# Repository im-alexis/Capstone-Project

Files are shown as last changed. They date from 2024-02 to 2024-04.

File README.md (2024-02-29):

# Capstone Project
# Autonomous Plant Watering System Senior Design

Faculty Mentor: Dr. Wei Li

Team Members: Javier Padilla, Alexis Torres, Ian Skillman, Kiet Le, Evan LeBel, Jesus Hernandez, Jaime Sanchez, Rodrigo Romero

Project Description:
Due to changes in the weather and busy work weeks, it can be challenging to keep track of when you last watered your plants. Our Watering System will automate the need to keep track of the last time you watered your plants and give you more time to enjoy seeing your plants grow. This can create longevity in plants including flowers and plants that can feed humans for years to come. 
Specifically, the project will focus on a single unit that contains a small to medium-sized plant. Attached to the unit will be multiple sensors that will detect/measure/record moisture, temperature, humidity, sunlight, and the water level of an in-unit source. Using a Web UI, the user will be able to manually control and set custom watering settings for the unit. 

Team Composition
4 software engineers developing the software that will use algorithms to automate the watering system based on conditions received from the sensors. All of which can be monitored and manually activated on a remote Web UI. 
3 embedded systems engineers working on communication between sensors and microcontroller, as well as any drivers necessary for the attached LCD display or features that are going to be added. Adding additional electronics to power the microcontroller (including a battery pack and solar cell)

Objectives
Embedded Systems Development: Efficient and reliable embedded systems that control hardware components and devices.
Firmware and Software Development: Creating software and firmware to control and interact with hardware components, creating communication with full functionality.
Networking and Communication: Designing systems that can communicate with each other using various communication protocols (TCP or UDP), such as Wi-Fi or Bluetooth.
Test and Validation: Develop test plans and methodologies to ensure that the designed systems and components meet performance and reliability requirements.
Usability and User Experience: Design software interfaces that are user-friendly experience for end-users.
Scalability and Performance: Build software that can handle increased user loads and data info while maintaining optimal performance.
Compatibility: Develop software that is compatible with multiple devices, operating systems, and browsers, to ensure consistent user experience across platforms.
Code Reviews: Collaborative code reviews to maintain code quality, pass knowledge, and resolve code-related issues.
Documentation: Create comprehensive documentation to outline software functionality, architecture, APIs, and usage guidelines.
Data Management: Design a robust data management system to ensure data integrity for software data storage and processing.
Teams
Embedded Systems Team:

Members: Ian Skillman, Evan LeBel, and Jaime Sanchez
Subsystems: Plant Microcontroller, Hub, Wireless, PCB Design
Roles: Firmware/Software, PCB Designer, Hardware Test/Validation, RF, Power, and Data Packet design
Members: 
Ian     - Sensors communication and plant Micro and Water Mechanics
	Evan  - Plant info and Water Mechanics/System Designer/HUB Master/PCB design
	Jaime - Communications/PCB design
Team Timeline:
Checkpoint 1: APIs - TBD
Checkpoint 2: Plant Microcontroller  - TBD
Checkpoint 3: Hub Microcontroller - TBD
Checkpoint 4: Plant-Hub Communication - TBD 
Checkpoint 5: Water Mechanics Design  - TBD
Checkpoint 6: Custom PCB Schematics - TBD 
Checkpoint 7: Final Casing/Housing - TBD

Design Idea:
A plant module will have 3 attached sensors: Light, moisture, and temperature. These sensors will communicate with a custom PCB where the microcontroller will be located. Each plant will have its own sensors and microcontroller, but can also be expanded to accommodate multiple plants per microcontroller. The microcontroller will periodically read the sensors and, based on the sensor data, enable or disable a water pump that delivers water into the plant's soil. The water flow will be fixed, with the amount of water released determined by a time-based factor. The water pump will be connected to a water tank equipped with a sensor to monitor the water level within the tank. This sensor will communicate with the hub, which will be responsible for broadcasting notifications regarding the need to refill the tank. Each microcontroller will communicate with the hub via Bluetooth to periodically send current sensor readings from the plants. The hub can receive multiple data packets from various microcontrollers. Bluetooth will utilize the TCP protocol to prevent interference. The hub will then relay the received data packets over Wi-Fi to be accessed by the PC user for reading and analysis.

Demonstrations of multiple Plant modules per tank/HUB

Software Team: Web Development

Members: Alexis Torres, Kiet Le, Javier Padilla, and Jesus Hernandez
Subsystems: Server / UI - Backend/Front End
Roles:
	Front End Dev: Alexis Torres and Javier Padilla
	Backend Dev: Kiet Le and Jesus Hernandez
Description:
The software team's primary responsibility involves developing the web application, which serves as the user interface for the project. This entails creating a comprehensive, full-stack application capable of storing both user and plant data. Additionally, the software team will manage the critical communication link between the user and the microcontroller.

To ensure a seamless user experience, the team will focus on crafting an intuitive and user-friendly interface, accompanied by an aesthetically pleasing user interface design.

Requirements: 
User Friendly UI
Dark/Light Mode
Language Setting
English
Spanish
Etc.
Account System
Admin Level Control
System Customization
Manual Control
Adding and Configuring Plant Profile
Standard User Level
Monitoring 
Monitoring
Graphical Sensor Data Display
Water Level
Light Detection
Moisture Level
Etc.
System Settings Customization
Custom Plant Profiles
Water Needs
Lights Needs
Data Transmission Rate
New Plant Integration
History
Saving Packets Received from the system
Maintaining History of Notification Events / System Events
Notifications 
SMS
Email
Upscale:
App Development:
Convert the web app into a mobile app that can be accessed on both IOS and Android. 
System Design Draft:
<INPUT PROJECT NAME>
Project Description: <NEEDS WORK>

Team Composition
4 software engineers developing the software that will use algorithms to automate the watering system based on conditions received from the sensors. All of which can be monitored and manually activated on a remote Web UI. 
3 embedded systems engineers working on communication between sensors and microcontroller, as well as any drivers necessary for the attached LCD display or features that are going to be added. Adding additional electronics to power the microcontroller (including a battery pack and solar cell)
Objectives <Fill in Data>
Teams
Embedded Systems Team: <NEED WORK>

Members: Ian Skillman, Evan LeBel, and Jaime Sanchez
Subsystems: Plant Microcontroller, Hub, Wireless, PCB Design
Roles: Firmware/Software, PCB Designer, Hardware Test/Validation, RF, Power, and Data Packet design
Members: 
Ian     - 
	Evan  - 
	Jaime - 
Team Timeline:
Software Team: Web Development

Members: Alexis Torres, Kiet Le, Javier Padilla, and Jesus Hernandez
Subsystems: Server / UI - Backend/Front End
Roles:
	Front End Dev: Alexis Torres and Javier Padilla
	Backend Dev: Kiet Le and Jesus Hernandez
Description:
The software team's primary responsibility involves developing the web application, which shall function as a tool for doctors to monitor patient’s health. This entails creating a comprehensive, full-stack application capable of storing both user and sensor data. Additionally, the software team will manage the critical communication link between the user and the microcontroller. 

To ensure a seamless user experience, the team will focus on crafting an intuitive and user-friendly interface, accompanied by an aesthetically pleasing user interface design.

The goal is to set a framework for health monitoring, where more wearable devices can interface with the web application.  

Requirements: 
User Friendly UI
Dark/Light Mode
Language Setting
English
Spanish
Etc.
Account System
Admin/ Doctor Level Control
System Customization
Manual Control
Adding and Configuring Patient Profile
Standard User Level
Monitoring their own device data
Monitoring
Graphical Sensor Data Display

Etc.
System Settings Customization
Data Transmission Rate
New device integration
History
Saving Packets Received from the system
Maintaining History of Notification Events / System Events
Notifications 
SMS
Email

Upscale:
App Development:
Convert the web app into a mobile app that can be accessed on both IOS and Android. 
Interface for health monitoring wearable devices

System Design Draft:

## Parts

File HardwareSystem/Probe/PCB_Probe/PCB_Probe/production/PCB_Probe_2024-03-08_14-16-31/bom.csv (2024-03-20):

Designator | Footprint | Quantity | Value | LCSC Part #
BT1 | BAT_BH9VPC | 1 | BH9VPC
C1, C10, C9 | C_Disc_D4.7mm_W2.5mm_P5.00mm | 3 | 100nF
C2 | C_Disc_D4.7mm_W2.5mm_P5.00mm | 1 | 10nF
C3 | C_Disc_D4.7mm_W2.5mm_P5.00mm | 1 | 470pF
C4 | C_Disc_D4.7mm_W2.5mm_P5.00mm | 1 | 10uF
D1 | D_DO-35_SOD27_P7.62mm_Horizontal | 1 | 1N4148
H1, H2, H3, H4, H5 | MountingHole_3.2mm_M3 | 5 | MountingHole
J1, J2 | PRT16279 | 2 | Conn_01x15
J3 | PinHeader_1x02_P2.54mm_Vertical | 1 | Conn_01x02_Socket
J4 | PinHeader_1x04_P2.54mm_Vertical | 1 | Conn_01x04_Pin
R1 | R_Axial_DIN0207_L6.3mm_D2.5mm_P10.16mm_Horizontal | 1 | 330R
R2 | R_Axial_DIN0207_L6.3mm_D2.5mm_P10.16mm_Horizontal | 1 | 1.6kR
R3, R6 | R_Axial_DIN0207_L6.3mm_D2.5mm_P10.16mm_Horizontal | 2 | 10kR
R4 | R_Axial_DIN0207_L6.3mm_D2.5mm_P10.16mm_Horizontal | 1 | 1MF
TP1 | TestPoint_Pad_D1.0mm | 1 | 9V Testpoint
TP2 | TestPoint_Pad_D1.0mm | 1 | 3.3V Testpoint
TP4 | TestPoint_Pad_D1.0mm | 1 | 3.3V GND Testpoint
TP5 | TestPoint_Pad_D1.0mm | 1 | Mouisture Testpoint
TP6 | TestPoint_Pad_D1.0mm | 1 | Light Testpoint
U1 | DIP-8_W7.62mm | 1 | TLC555xP

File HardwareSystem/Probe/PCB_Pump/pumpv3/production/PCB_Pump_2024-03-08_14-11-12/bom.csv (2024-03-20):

Designator | Footprint | Quantity | Value | LCSC Part #
5V, 9V, GND | TestPoint_Keystone_5000-5004_Miniature | 3 | TestPoint_Keystone_5000-5004_Miniature
A2 | Arduino_Nano_ESP32_Socket | 1 | Arduino_Nano_ESP32_Socket
C1 | C_Axial_L5.1mm_D3.1mm_P7.50mm_Horizontal | 1 | 0.22 uF
C2 | C_Axial_L5.1mm_D3.1mm_P7.50mm_Horizontal | 1 | 0.1 uF
C3 | C_Axial_L3.8mm_D2.6mm_P7.50mm_Horizontal | 1 | 1nF
C4, C5, C6 | CP_Radial_Tantal_D6.0mm_P2.50mm | 3 | 100uF
D1 | D_DO-35_SOD27_P7.62mm_Horizontal | 1 | 1N914
D2 | D_DO-41_SOD81_P10.16mm_Horizontal | 1 | 1N5819
D3 | D_DO-41_SOD81_P10.16mm_Horizontal | 1 | 1N5817
J1, J2 | PinHeader_1x04_P2.54mm_Vertical | 2 | Conn_01x04_Pin
L1 | L_Axial_L7.0mm_D3.3mm_P10.16mm_Horizontal_Fastron_MICC | 1 | 1000uH
P1_2, P1, P2 | PinHeader_1x02_P2.54mm_Vertical | 3 | PinHeader_1x02_P2.54mm_Vertical
Q1 | IRF510PBF | 1 | IRF510
Q2 | TO-220-3_Vertical | 1 | IRF4905
R1 | R_Axial_DIN0207_L6.3mm_D2.5mm_P7.62mm_Horizontal | 1 | 12k
R2 | R_Axial_DIN0207_L6.3mm_D2.5mm_P7.62mm_Horizontal | 1 | 0.22
R3 | R_Axial_DIN0207_L6.3mm_D2.5mm_P7.62mm_Horizontal | 1 | 180
R4 | R_Axial_DIN0207_L6.3mm_D2.5mm_P7.62mm_Horizontal | 1 | 6.2K
R5 | R_Axial_DIN0207_L6.3mm_D2.5mm_P7.62mm_Horizontal | 1 | 1k
R6 | R_Axial_DIN0207_L6.3mm_D2.5mm_P7.62mm_Horizontal | 1 | 10K
TP1 | TP4056-18650 | 1 | TP4056
U2 | DIP-8_W7.62mm | 1 | MC33063AP
U3 | TO-220-3_Vertical | 1 | LM7805_TO220

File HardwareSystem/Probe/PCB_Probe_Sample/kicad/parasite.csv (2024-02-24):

Comment | Designator | Footprint | LCSC
Battery_Cell | BT1 | kicad:BatteryHolder_Keystone_3002_1x2032
1n | C1 | Capacitor_SMD:C_0402_1005Metric | C1523
100n | C2 | Capacitor_SMD:C_0402_1005Metric | C1525
12p | C3,C4 | Capacitor_SMD:C_0402_1005Metric | C1547
LL4148 | D1 | Diode_SMD:D_MiniMELF | C9808
LED | D2 | LED_SMD:LED_0603_1608Metric | C2286
MMBT3906 | Q1 | Package_TO_SOT_SMD:SOT-23 | C2910191
Q_Photo_NPN | Q4 | snapeda:TR8 | C146233
10k | R1,R4,R7,R8 | Resistor_SMD:R_0402_1005Metric | C25744
470 | R10 | Resistor_SMD:R_0402_1005Metric | C25117
1k | R2 | Resistor_SMD:R_0402_1005Metric | C11702
1M | R6 | Resistor_SMD:R_0402_1005Metric | C26083
B3U-1000P | RST1,SW1 | SW_B3U-1000P | C231329
E73-2G4M08S1C | U1 | snapeda:E73-2G4M08S1C | C356849
SHTC3 | U2 | kicad:Sensirion_DFN-4-1EP_2x2mm_P1mm_EP0.7x1.6mm | C194656
32.768kHz | Y1 | Crystal:Crystal_SMD_3215-2Pin_3.2x1.5mm | C32346

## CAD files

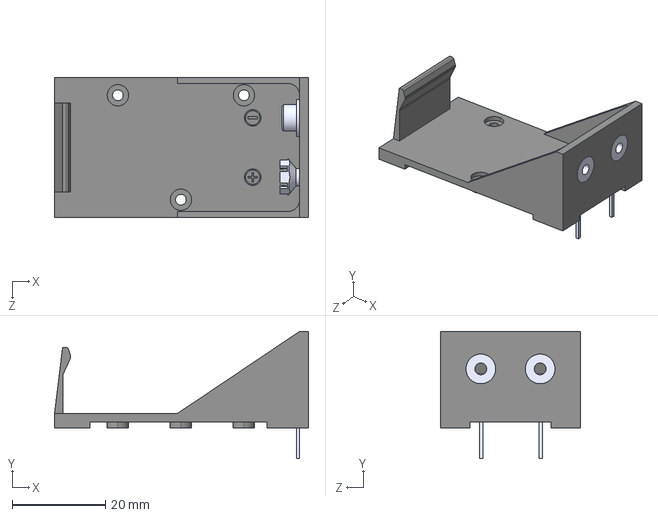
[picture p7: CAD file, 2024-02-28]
HardwareSystem/Probe/Component Library/BH9VPC/BH9VPC.step
54.4 x 27.2 x 30.0 mm

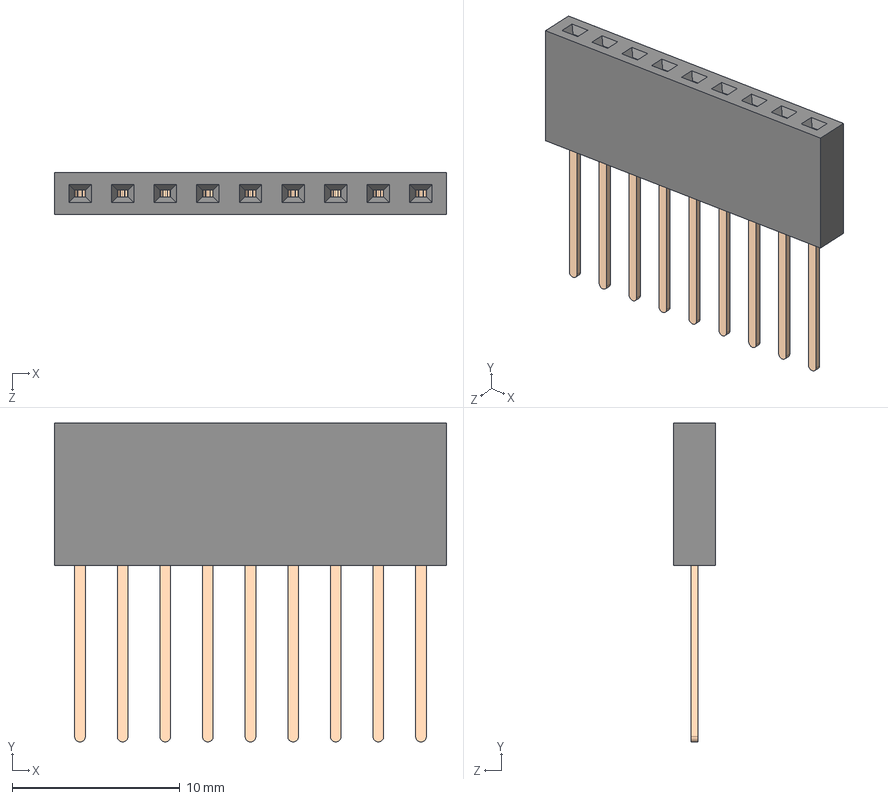
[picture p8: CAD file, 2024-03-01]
HardwareSystem/Probe/Component Library/Headers-PRT-16279/3D/PRT-16279.stp
23.4 x 19.0 x 2.50 mm

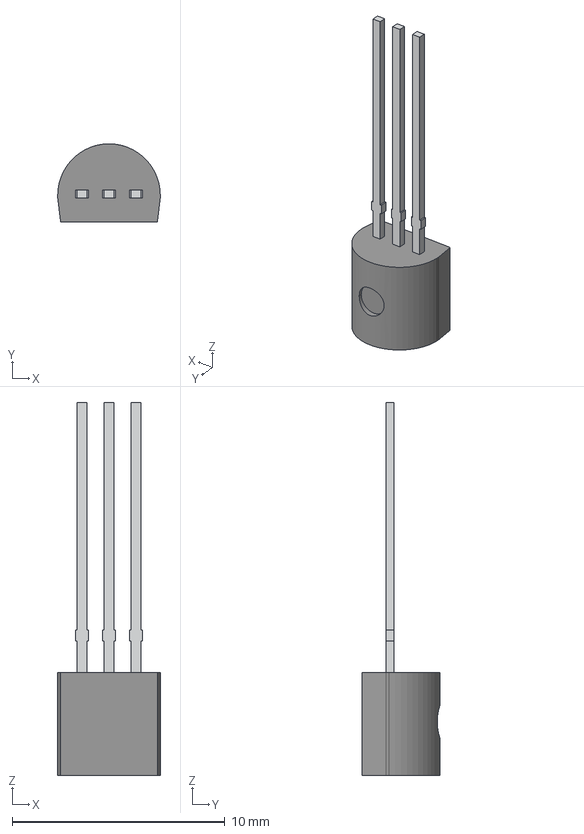
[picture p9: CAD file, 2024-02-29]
HardwareSystem/Probe/Component Library/LP2950CZ_3_0_NOPB/LP0003A.stp
4.83 x 3.68 x 17.5 mm
BODY-TO92
LEAD-TO92 x 3

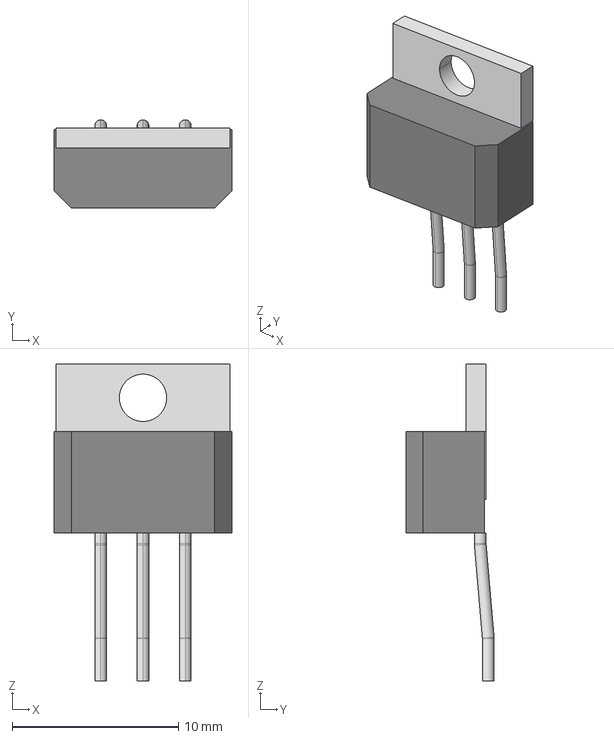
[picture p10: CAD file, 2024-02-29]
HardwareSystem/Probe/Component Library/MCP1825S_3002E_AB/TO-220_AB_MC_MCH.step
10.7 x 5.31 x 19.1 mm

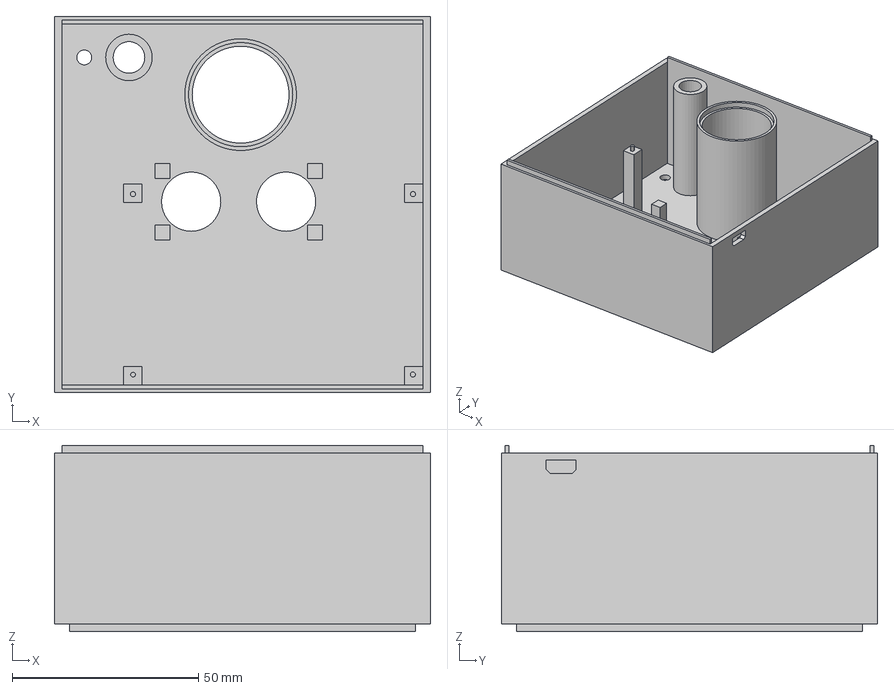
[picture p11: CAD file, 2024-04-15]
HardwareSystem/Probe/Component Library/New_bottom_half.3mf
101.0 x 101.0 x 50.0 mm

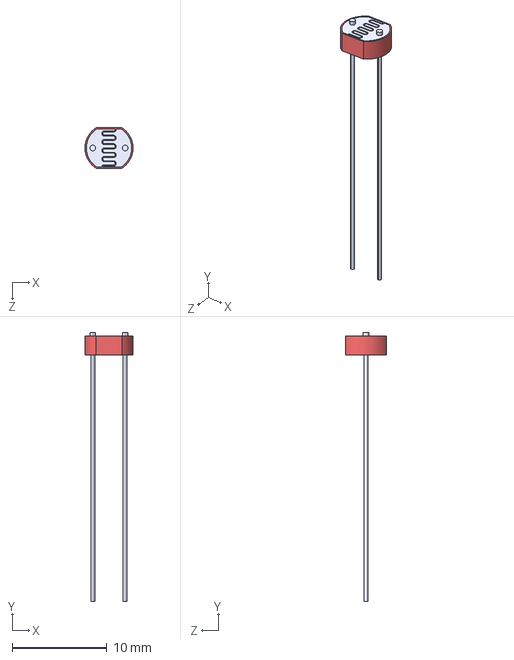
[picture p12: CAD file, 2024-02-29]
HardwareSystem/Probe/Component Library/Photoresistor-161/161.step
5.07 x 28.4 x 4.29 mm

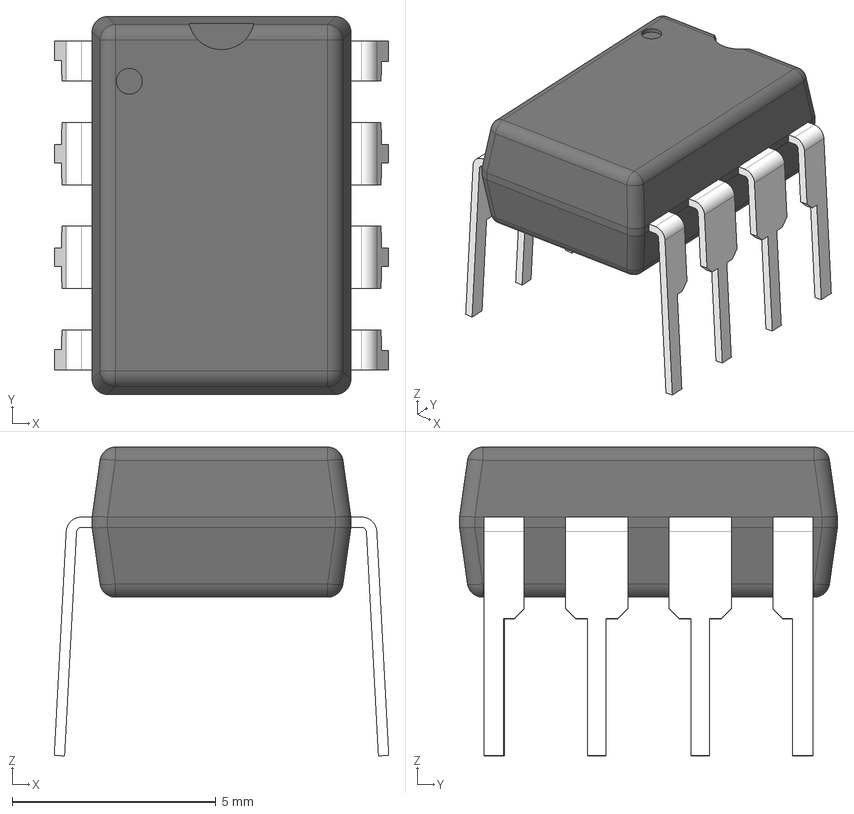
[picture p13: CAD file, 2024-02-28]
HardwareSystem/Probe/PCB_Probe/PCB_Probe/models/ti_TLV5618AIP.stp
8.20 x 9.27 x 7.58 mm
BODY_P0008A
LEAD_P0008A x 4
LD_LHALF_P0008A x 2
LD_RHALF_P0008A x 2

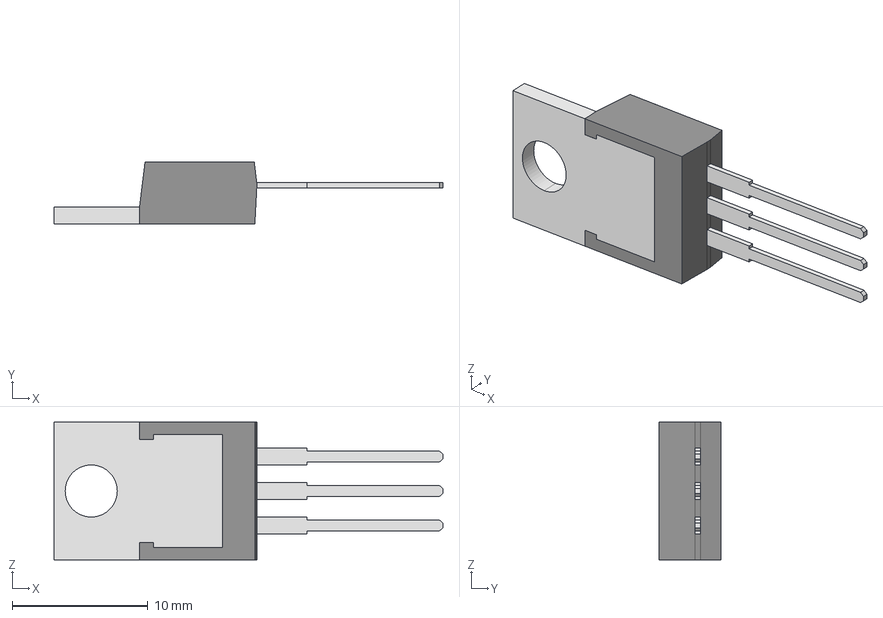
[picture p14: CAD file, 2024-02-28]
HardwareSystem/Probe/PCB_Probe/PCB_Probe/models/LM7805CT_NOPB.stp
28.7 x 4.57 x 10.2 mm
T03B_BODY
T03B_LEAD x 3
T03B_HS

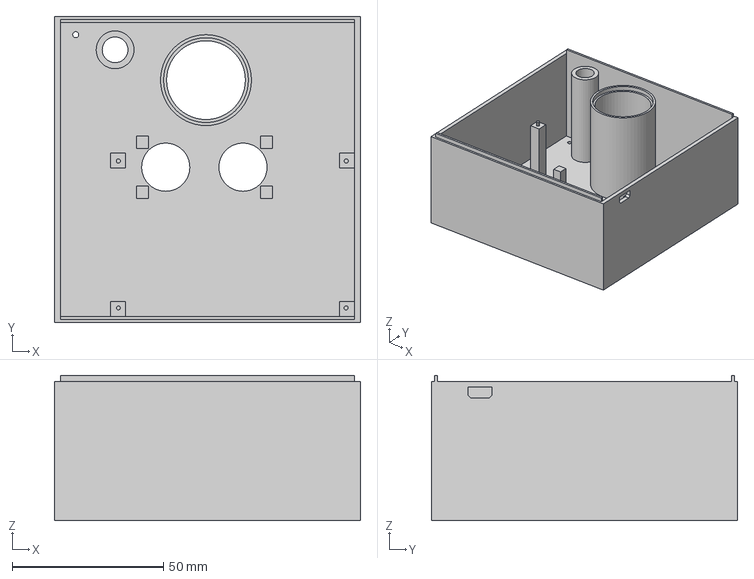
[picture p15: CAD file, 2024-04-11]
HardwareSystem/Probe/Component Library/Hub_Bottom.3mf
101.0 x 101.0 x 48.0 mm

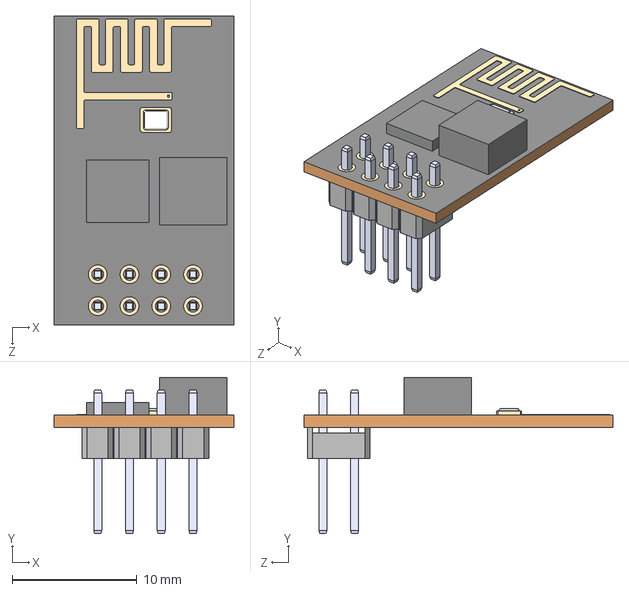
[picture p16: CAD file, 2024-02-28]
HardwareSystem/Probe/PCB_Probe/PCB_Probe/models/ai_thinker_ESP8266-01.step
14.4 x 12.5 x 24.7 mm

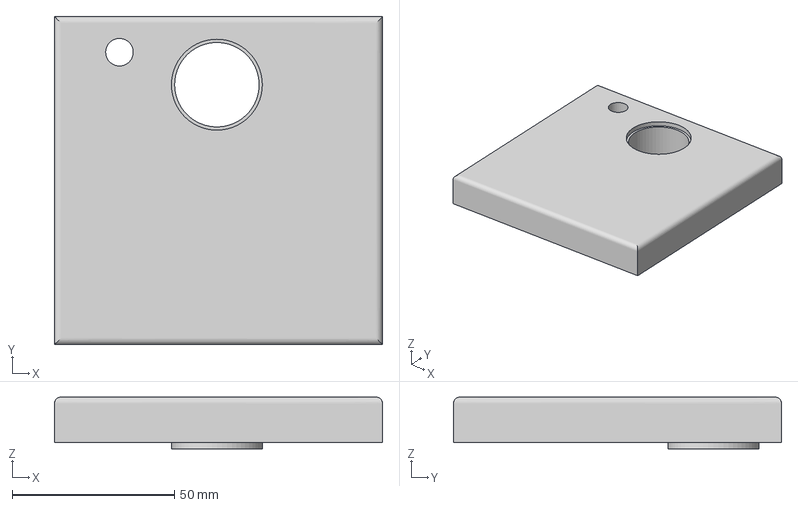
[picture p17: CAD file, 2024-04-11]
HardwareSystem/Probe/Component Library/Hub_Top.3mf
101.0 x 101.0 x 16.0 mm

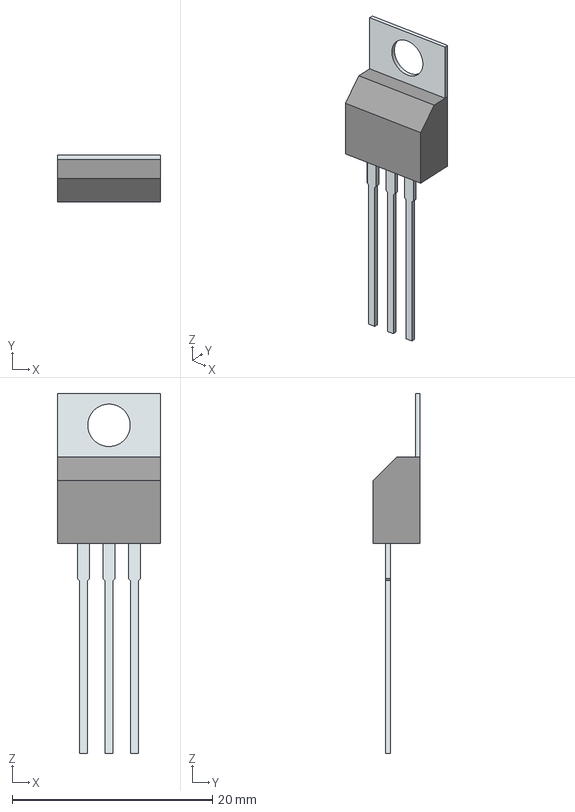
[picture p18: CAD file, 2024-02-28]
HardwareSystem/Probe/PCB_Probe/PCB_Probe/models/LM2937ET-3.3_NOPB.stp
10.3 x 4.70 x 35.9 mm
Tab
PinsArray

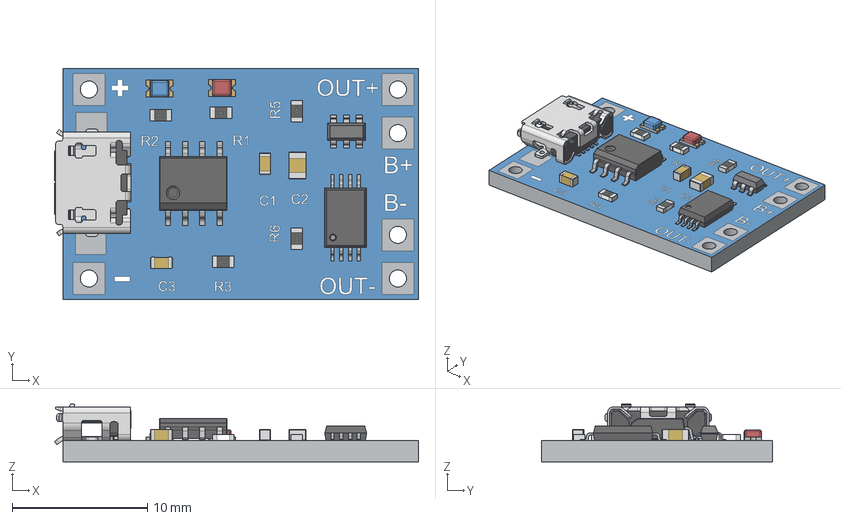
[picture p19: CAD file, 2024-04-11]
HardwareSystem/Probe/Component Library/Lipo Charger - With Load Protection.stp
26.9 x 17.1 x 4.28 mm
bOARD
0603 Capacitor x 2
0603 Resistor x 5
0805 Capacitor
SOIC-8-150
LED - 0805 - Blue
LED - 0805 - Red
USB - Micro
tsop8
sot-23-6-2

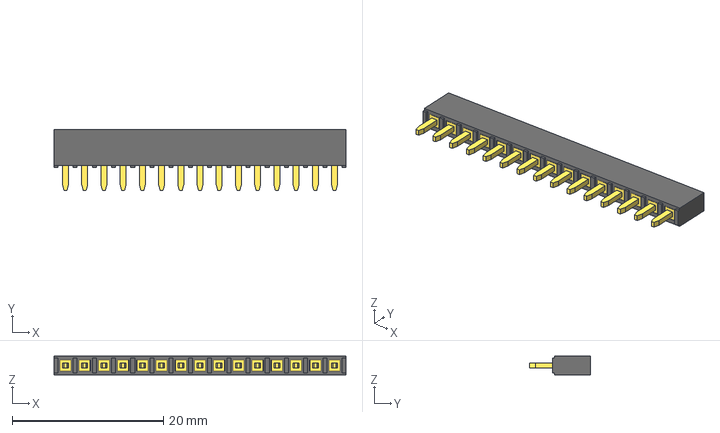
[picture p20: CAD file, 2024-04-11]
HardwareSystem/Probe/Component Library/15-Pin Header - Female - 2.54mm.step
38.6 x 8.00 x 2.50 mm

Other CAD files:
HardwareSystem/Probe/Component Library/Hub_Bottom_Walls.3mf
HardwareSystem/Probe/PCB_Probe/PCB_Probe/models/ti_LM4041CILPR.step
HardwareSystem/Probe/PCB_Probe/PCB_Probe/models/adafruit_st7735r.stp
HardwareSystem/Probe/PCB_Probe/PCB_Probe/models/vishay_IRLD024PBF.stp
HardwareSystem/Probe/Component Library/Hub_Bottom.stl
HardwareSystem/Probe/PCB_Probe/PCB_Probe/models/COM-16473.stp

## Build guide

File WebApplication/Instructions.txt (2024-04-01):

ALWAYS WORK IN A VIRTUAL ENVIRONMENT - When Developing backend

TO CREATE A VIRTUAL ENVIRONMENT: (pip or pip3)
pip install virtualenv
python<version> -m venv <virtual-environment-name>

TO ACTIVATE THE ENVIRONMENT:
source <virtual-environment-name>/bin/activate

TO INSTALL LIBRARIES:
pip install -r requirements.txt  

IF YOU ADD NEW LIBRARIES:
pip freeze > requirements.txt

TO CLOSE THE VIRTUAL ENVIRONMENT:
deactivate

DATABASE AND ROUTES DEFINITION
https://docs.google.com/document/d/1mbG9H52PVBVGft23lnzvOi_USRNvHaWslcnwI_Q0cF0/edit?usp=sharing

TO START backend
cd WebApplication/backend
flask --app app run

TO START frontend
cd WebApplication/frontend/apws
npm start

To Test With HARDWARE
Launch backend using python app.py

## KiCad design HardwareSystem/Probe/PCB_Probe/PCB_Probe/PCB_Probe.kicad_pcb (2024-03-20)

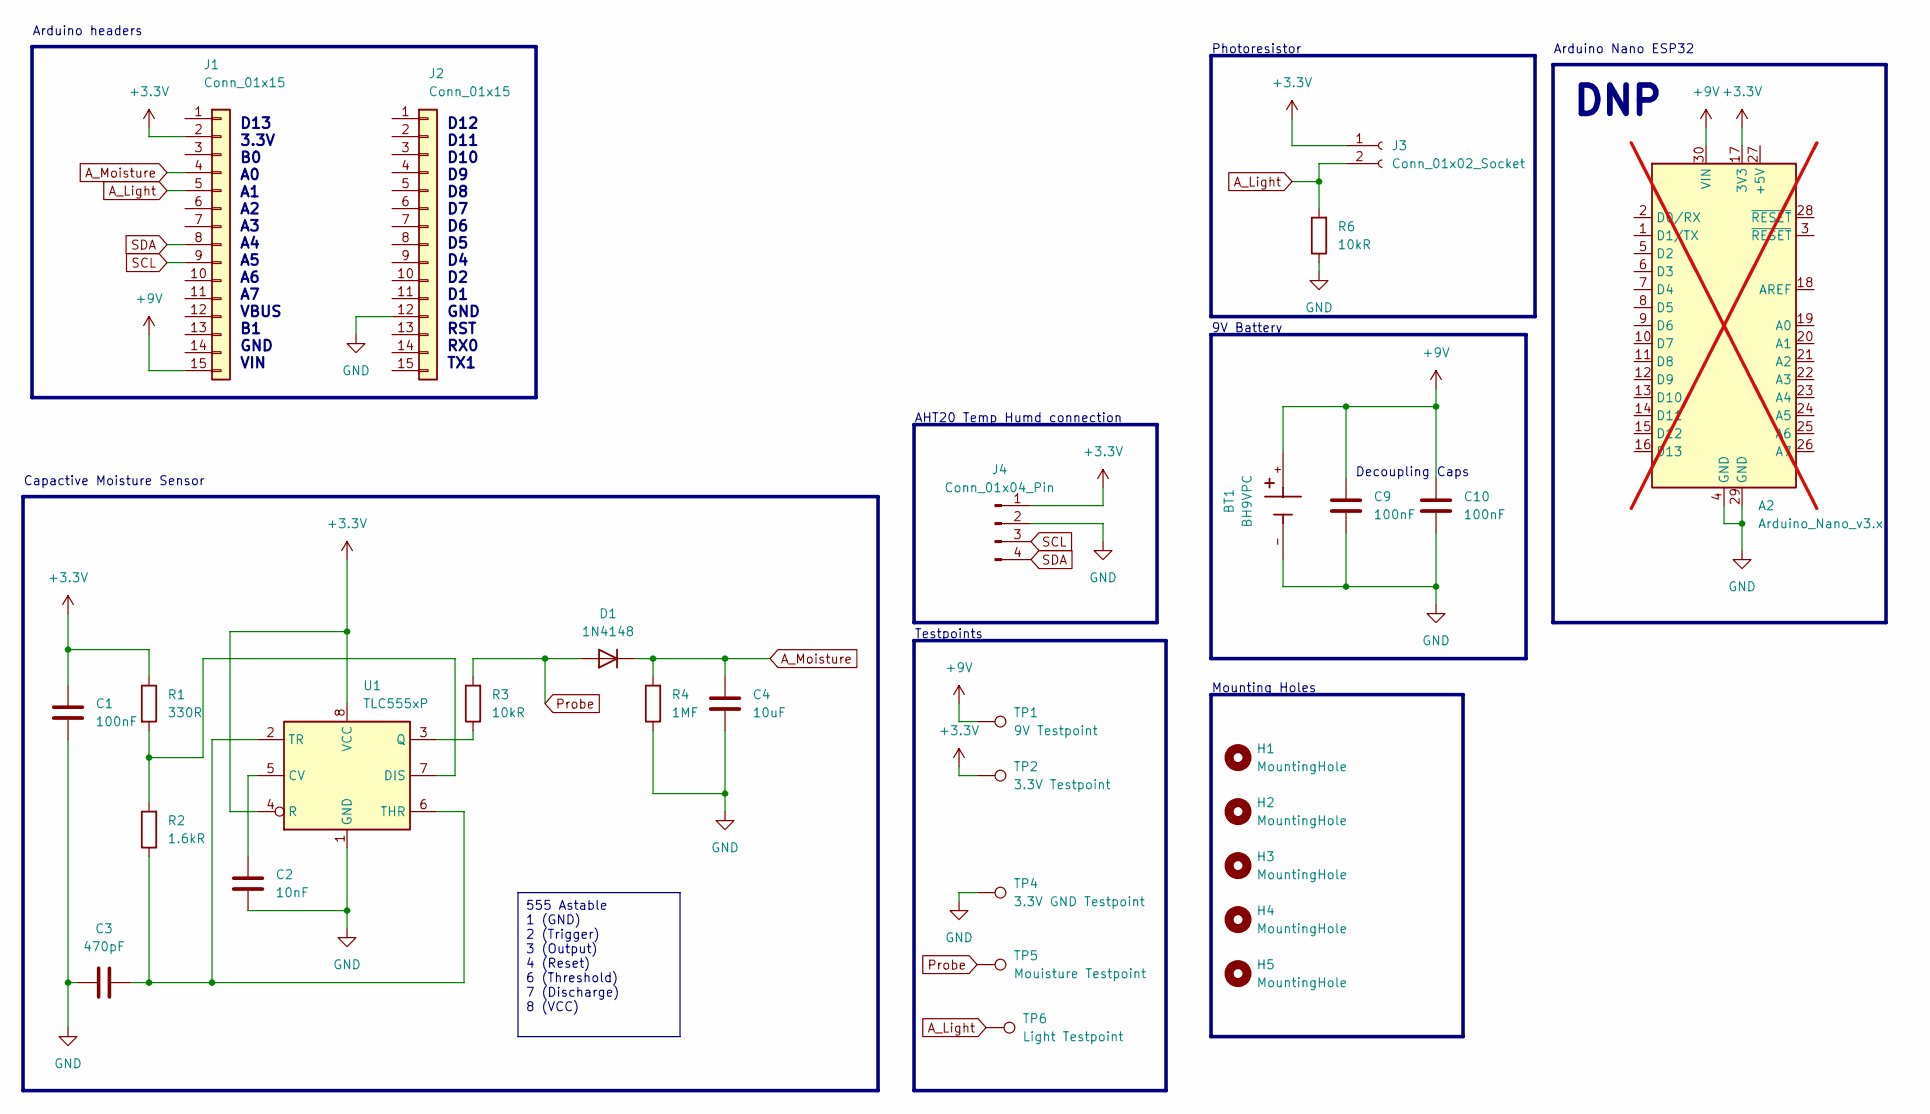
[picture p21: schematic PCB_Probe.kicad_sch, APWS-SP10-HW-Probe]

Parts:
A2: Arduino_Nano_v3.x; Arduino_Nano; not fitted
BT1: BH9VPC; BAT_BH9VPC; PARTREV F
C1, C9, C10: 100nF; C_Disc_D4.7mm_W2.5mm_P5.00mm
C2: 10nF; C_Disc_D4.7mm_W2.5mm_P5.00mm
C3: 470pF; C_Disc_D4.7mm_W2.5mm_P5.00mm
C4: 10uF; C_Disc_D4.7mm_W2.5mm_P5.00mm
D1: 1N4148; D_DO-35_SOD27_P7.62mm_Horizontal
H1, H2, H3, H4, H5: MountingHole; MountingHole_3.2mm_M3
J1, J2: Conn_01x15; PRT16279
J3: Conn_01x02_Socket; PinHeader_1x02_P2.54mm_Vertical
J4: Conn_01x04_Pin; PinHeader_1x04_P2.54mm_Vertical
R1: 330R; R_Axial_DIN0207_L6.3mm_D2.5mm_P10.16mm_Horizontal
R2: 1.6kR; R_Axial_DIN0207_L6.3mm_D2.5mm_P10.16mm_Horizontal
R3, R6: 10kR; R_Axial_DIN0207_L6.3mm_D2.5mm_P10.16mm_Horizontal
R4: 1MF; R_Axial_DIN0207_L6.3mm_D2.5mm_P10.16mm_Horizontal
TP1: 9V Testpoint; TestPoint_Pad_D1.0mm
TP2: 3.3V Testpoint; TestPoint_Pad_D1.0mm
TP4: 3.3V GND Testpoint; TestPoint_Pad_D1.0mm
TP5: Mouisture Testpoint; TestPoint_Pad_D1.0mm
TP6: Light Testpoint; TestPoint_Pad_D1.0mm
U1: TLC555xP; DIP-8_W7.62mm

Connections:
+3.3V: A2.17 (3V3), C1.2, J1.2, J3.1, J4.1, R1.1, TP2.1, U1.4 (R), U1.8 (VCC)
+9V: A2.30 (VIN), BT1.+, C9.1, C10.1, J1.15, TP1.1
A_Light: J1.5, J3.2, R6.2, TP6.1
A_Moisture: C4.1, D1.1 (K), J1.4, R4.2
GND: A2.4 (GND), A2.29 (GND), BT1.-, C1.1, C2.2, C3.1, C4.2, C9.2, C10.2, J2.12, J4.2, R4.1, R6.1, TP4.1, U1.1 (GND)
unnamed: C2.1, U1.5 (CV)
unnamed: R1.2, R2.2, U1.7 (DIS)
unnamed: R3.1, U1.3 (Q)
unnamed: C3.2, R2.1, U1.2 (TR), U1.6 (THR)
Probe: D1.2 (A), R3.2, TP5.1
SCL: J1.9, J4.3
SDA: J1.8, J4.4

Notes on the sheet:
555 Astable 1 (GND) 2 (Trigger) 3 (Output) 4 (Reset) 6 (Threshold) 7 (Discharge) 8 (VCC)
9V Battery
AHT20 Temp Humd connection
DNP
Testpoints
Arduino Nano ESP32
D13 3.3V B0 A0 A1 A2 A3 A4 A5 A6 A7 VBUS B1 GND VIN
Arduino headers
Photoresistor
Mounting Holes
Capactive Moisture Sensor
Decoupling Caps
D12 D11 D10 D9 D8 D7 D6 D5 D4 D2 D1 GND RST RX0 TX1

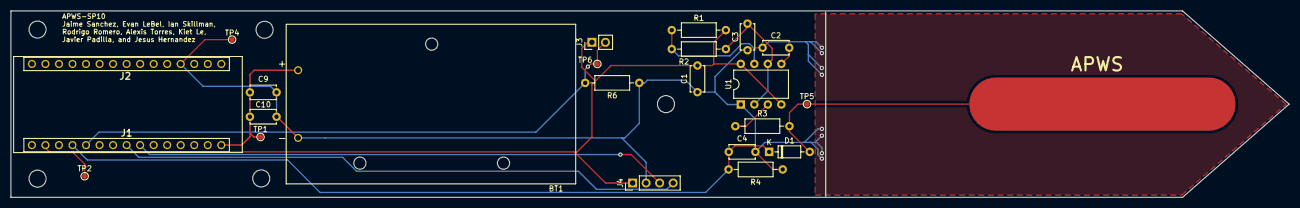
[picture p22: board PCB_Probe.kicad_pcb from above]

Board: 2 copper layers, 240.0 x 35.0 mm, 28 parts (0 on the bottom side), 12 nets.

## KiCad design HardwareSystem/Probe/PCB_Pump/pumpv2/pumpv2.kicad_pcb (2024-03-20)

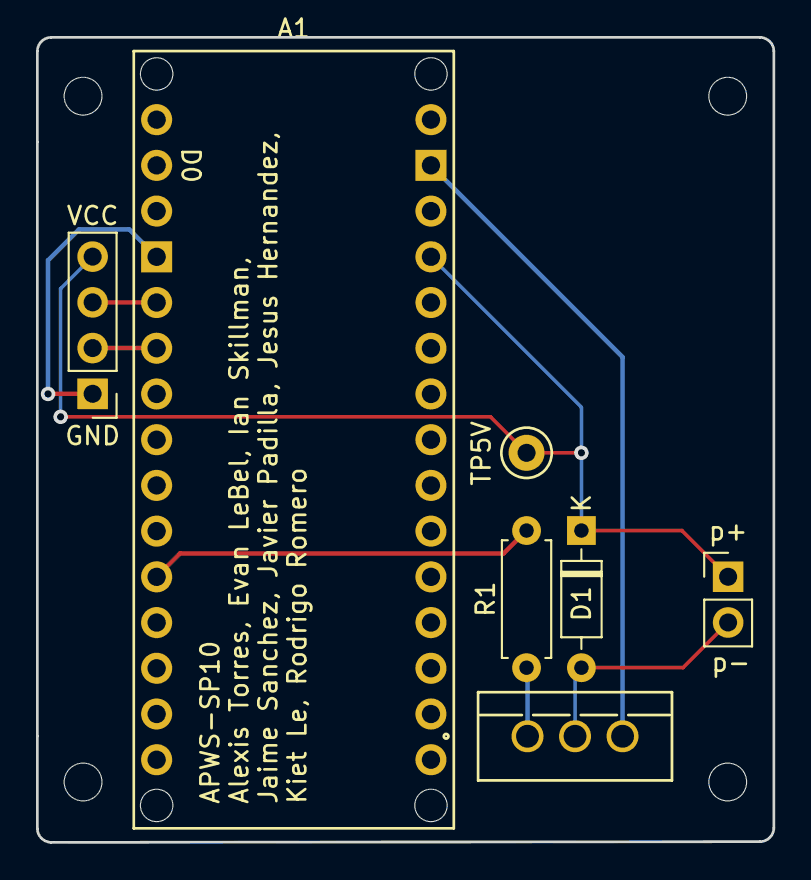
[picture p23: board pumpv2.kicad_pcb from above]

Board: 2 copper layers, 40.9 x 44.7 mm, 7 parts (0 on the bottom side), 5 nets.

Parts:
A1: Arduino_Nano_ESP32_Socket
D1: 1N914; D_DO-35_SOD27_P7.62mm_Horizontal
GND: Conn_01x04_Pin; PinHeader_1x04_P2.54mm_Vertical
Q1: IRF510; IRF510PBF
R1: 12k; R_Axial_DIN0207_L6.3mm_D2.5mm_P7.62mm_Horizontal
TP5V: TestPoint_Keystone_5000-5004_Miniature
p+: PinHeader_1x02_P2.54mm_Vertical

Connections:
GND: A1.GND1 (GND), A1.GND2 (GND), Q1.3 (S)
unnamed: A1.D8, R1.1
unnamed: Q1.1 (G), R1.2
pump+: A1.5V, D1.1 (K)
pump-: D1.2 (A), Q1.2 (D)

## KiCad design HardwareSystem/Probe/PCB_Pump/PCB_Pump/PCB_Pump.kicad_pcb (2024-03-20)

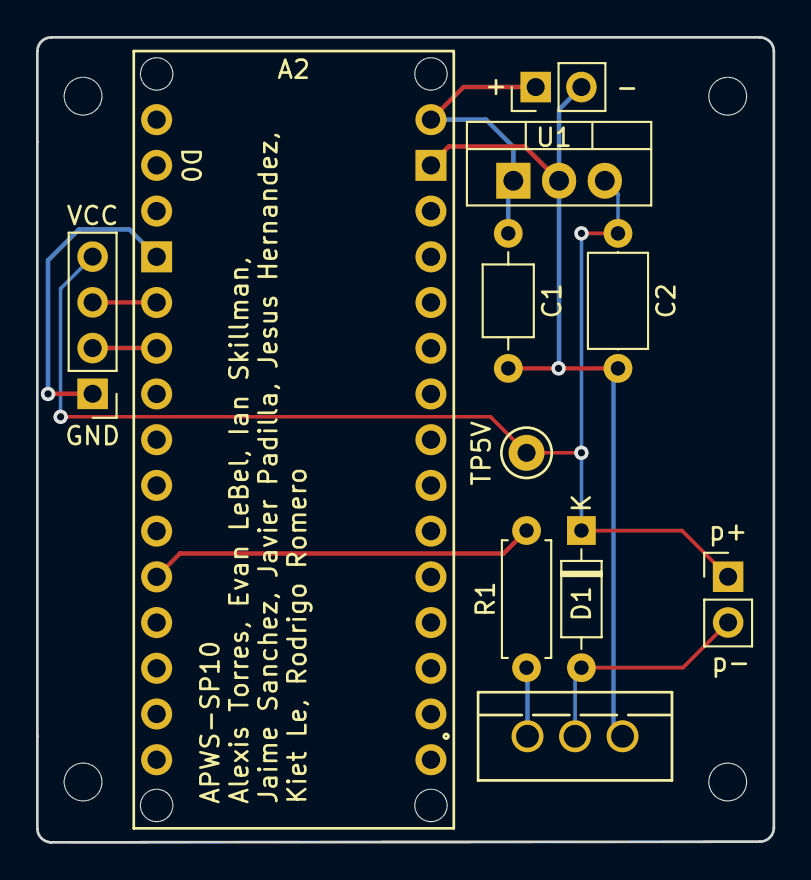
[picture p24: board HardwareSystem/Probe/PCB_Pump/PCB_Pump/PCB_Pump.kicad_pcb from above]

Board: 2 copper layers, 40.9 x 44.7 mm, 11 parts (0 on the bottom side), 8 nets.

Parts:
+: PinHeader_1x02_P2.54mm_Vertical
A2: Arduino_Nano_ESP32_Socket
C1: 0.1 uF; C_Axial_L3.8mm_D2.6mm_P7.50mm_Horizontal
C2: 10 uF; C_Axial_L5.1mm_D3.1mm_P7.50mm_Horizontal
D1: 1N914; D_DO-35_SOD27_P7.62mm_Horizontal
GND: Conn_01x04_Pin; PinHeader_1x04_P2.54mm_Vertical
Q1: IRF510; IRF510PBF
R1: 12k; R_Axial_DIN0207_L6.3mm_D2.5mm_P7.62mm_Horizontal
TP5V: TestPoint_Keystone_5000-5004_Miniature
U1: LM2937xT; TO-220-3_Vertical
p+: PinHeader_1x02_P2.54mm_Vertical

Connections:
9V: +.1, A2.VIN, C1.1, U1.1 (VI)
Echo: A2.D3, GND.2
GND: +.2, A2.GND1 (GND), A2.GND2 (GND), C1.2, C2.2, GND.1, Q1.3 (S), U1.2 (GND)
unnamed: A2.D8, R1.1
unnamed: Q1.1 (G), R1.2
Trig: A2.D2, GND.3
pump+: C2.1, D1.1 (K), GND.4, TP5V.1, U1.3 (VO), p+.1
pump-: D1.2 (A), Q1.2 (D), p+.2

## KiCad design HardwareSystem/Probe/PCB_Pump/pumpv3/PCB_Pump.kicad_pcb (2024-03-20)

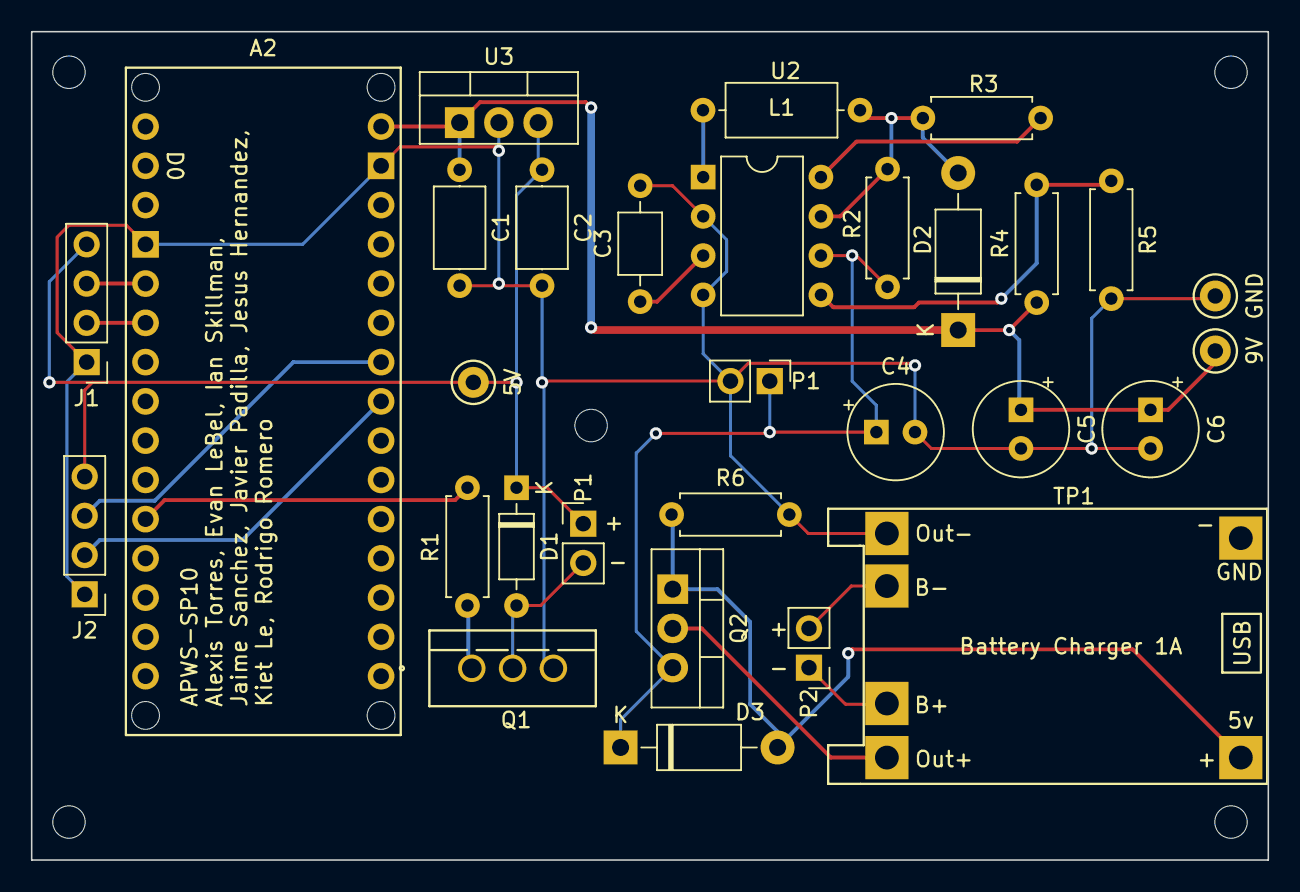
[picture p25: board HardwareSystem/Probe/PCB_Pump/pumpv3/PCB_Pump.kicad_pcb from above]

Board: 2 copper layers, 80.0 x 53.6 mm, 30 parts (0 on the bottom side), 20 nets.

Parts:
5V, 9V: TestPoint_Keystone_5000-5004_Miniature
A2: Arduino_Nano_ESP32_Socket
C1: 0.22 uF; C_Axial_L5.1mm_D3.1mm_P7.50mm_Horizontal
C2: 0.1 uF; C_Axial_L5.1mm_D3.1mm_P7.50mm_Horizontal
C3: 1nF; C_Axial_L3.8mm_D2.6mm_P7.50mm_Horizontal
C4, C5, C6: 100uF; CP_Radial_Tantal_D6.0mm_P2.50mm
D1: 1N914; D_DO-35_SOD27_P7.62mm_Horizontal
D2: 1N5819; D_DO-41_SOD81_P10.16mm_Horizontal
D3: 1N5817; D_DO-41_SOD81_P10.16mm_Horizontal
GND: TestPoint_Keystone_5000-5004_Miniature
J1, J2: Conn_01x04_Pin; PinHeader_1x04_P2.54mm_Vertical
L1: 1000uH; L_Axial_L7.0mm_D3.3mm_P10.16mm_Horizontal_Fastron_MICC
P1, P1#2, P2: PinHeader_1x02_P2.54mm_Vertical
Q1: IRF510; IRF510PBF
Q2: IRF4905; TO-220-3_Vertical
R1: 12k; R_Axial_DIN0207_L6.3mm_D2.5mm_P7.62mm_Horizontal
R2: 0.22; R_Axial_DIN0207_L6.3mm_D2.5mm_P7.62mm_Horizontal
R3: 180; R_Axial_DIN0207_L6.3mm_D2.5mm_P7.62mm_Horizontal
R4: 6.2K; R_Axial_DIN0207_L6.3mm_D2.5mm_P7.62mm_Horizontal
R5: 1k; R_Axial_DIN0207_L6.3mm_D2.5mm_P7.62mm_Horizontal
R6: 10K; R_Axial_DIN0207_L6.3mm_D2.5mm_P7.62mm_Horizontal
TP1: TP4056; TP4056-18650
U2: MC33063AP; DIP-8_W7.62mm
U3: LM7805_TO220; TO-220-3_Vertical

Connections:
3V7+: C4.1, D3.1 (K), P1#2.1, Q2.3 (S), R2.2, U2.6 (Vin)
3V7-: A2.GND1 (GND), A2.GND2 (GND), C1.2, C2.2, C3.2, C4.2, C5.2, C6.2, GND.1, J1.1, J2.1, P1#2.2, Q1.3 (S), R5.2, R6.2, TP1.4 (out-), U2.2 (SwE), U2.4 (GND), U3.2 (GND)
9V: 9V.1, A2.VIN, C1.1, C5.1, C6.1, D2.1 (K), R4.1, U3.1 (VI)
Batt+: P2.1, TP1.5 (B+)
Batt-: P2.2, TP1.6 (B-)
Echo: A2.D3, J1.2
unnamed: A2.D8, R1.1
unnamed: D2.2 (A), L1.1, R2.1, R3.2, U2.7 (Ipk)
unnamed: D3.2 (A), Q2.1 (G), R6.1, TP1.1 (in+)
unnamed: Q1.1 (G), R1.2
unnamed: Q2.2 (D), TP1.3 (out+)
unnamed: R3.1, U2.8 (DC)
unnamed: L1.2, U2.1 (SwC)
unnamed: C3.1, U2.3 (TC)
P5: R4.2, R5.1, U2.5 (Vfb)
SCL: A2.A5 (A5/SCL), J2.3
SDA: A2.A4 (A4/SDA), J2.2
Trig: A2.D2, J1.3
pump+: 5V.1, C2.1, D1.1 (K), J1.4, J2.4, P1.1, U3.3 (VO)
pump-: D1.2 (A), P1.2, Q1.2 (D)

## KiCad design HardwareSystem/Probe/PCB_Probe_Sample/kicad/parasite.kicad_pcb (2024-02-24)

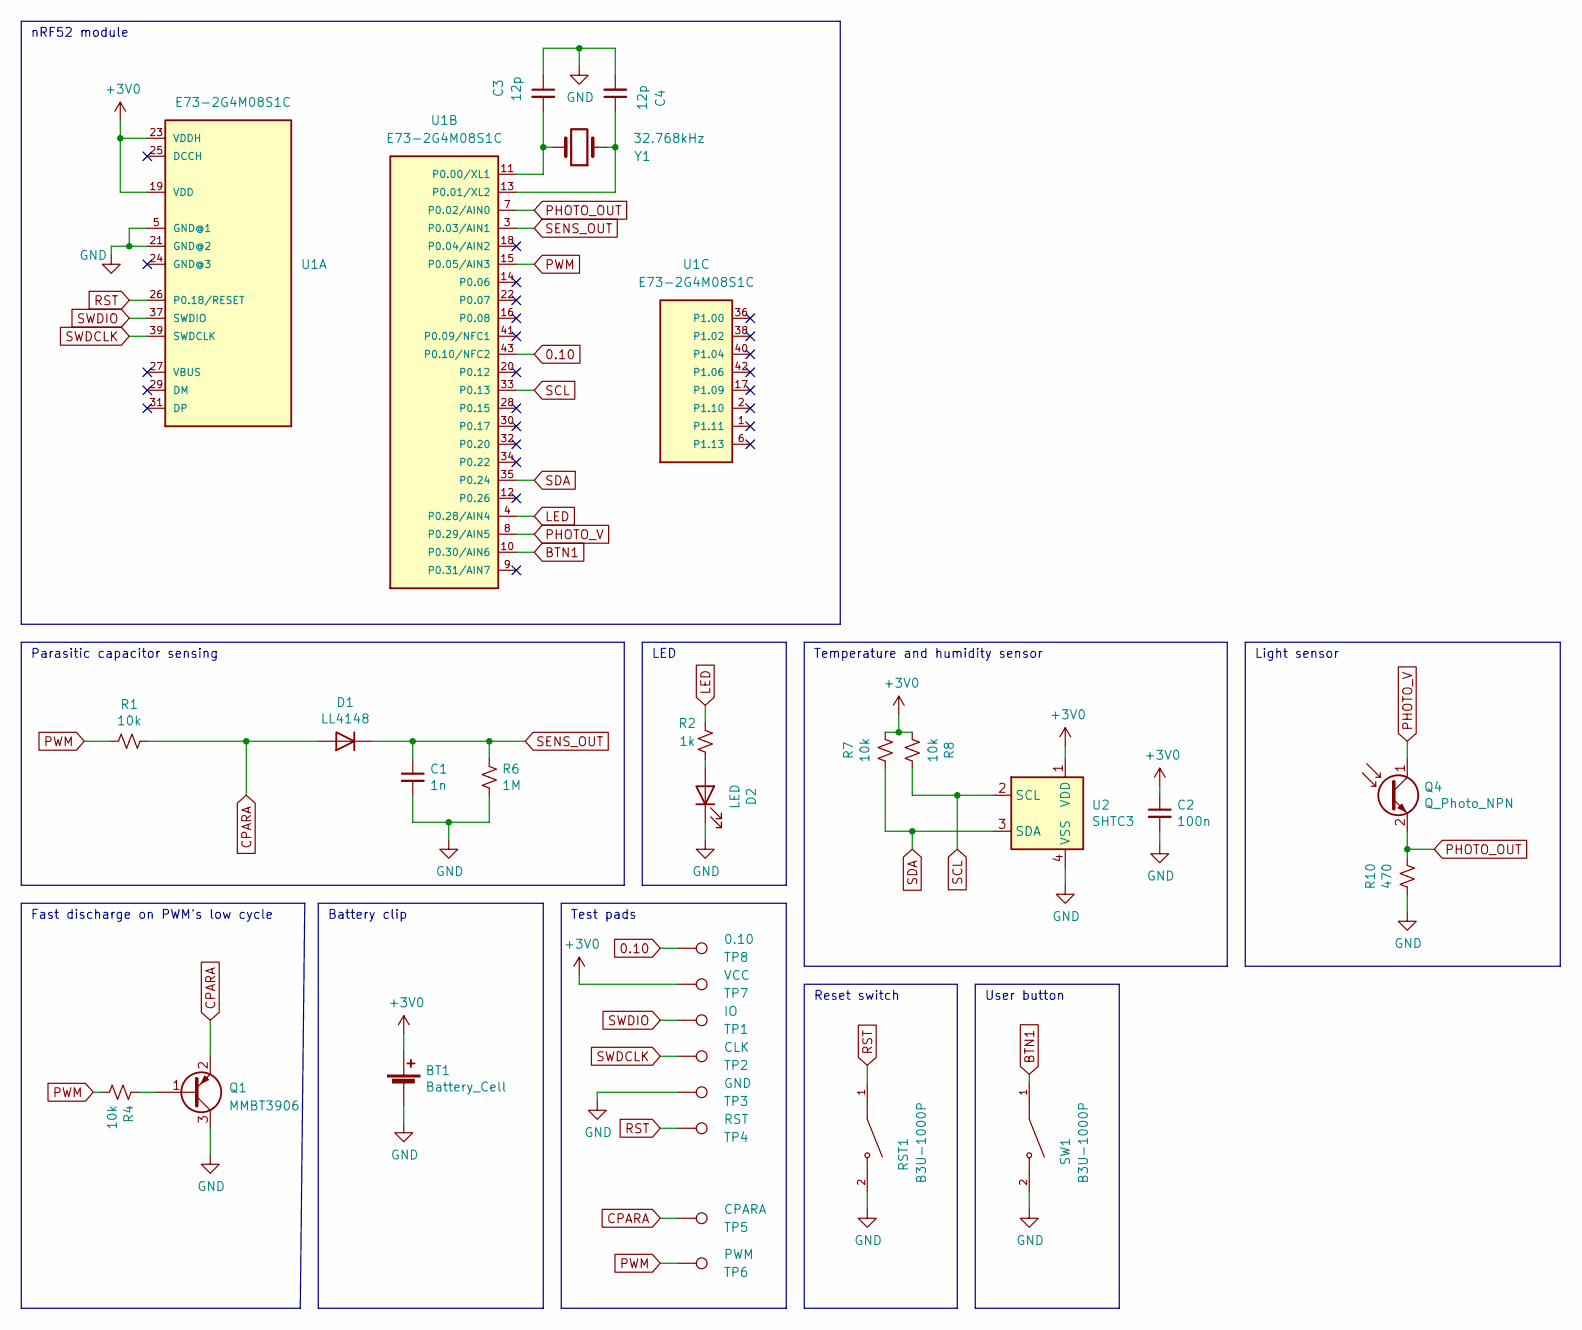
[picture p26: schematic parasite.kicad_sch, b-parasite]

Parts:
BT1: Battery_Cell; BatteryHolder_Keystone_3002_1x2032
C1: 1n; C_0402_1005Metric; LCSC C1523
C2: 100n; C_0402_1005Metric; LCSC C1525
C3, C4: 12p; C_0402_1005Metric; LCSC C1547
D1: LL4148; D_MiniMELF; LCSC C9808
D2: LED; LED_0603_1608Metric; LCSC C2286
Q1: MMBT3906; SOT-23; LCSC C2910191
Q4: Q_Photo_NPN; TR8; LCSC C146233
R1, R4, R7, R8: 10k; R_0402_1005Metric; LCSC C25744
R2: 1k; R_0402_1005Metric; LCSC C11702
R6: 1M; R_0402_1005Metric; LCSC C26083
R10: 470; R_0402_1005Metric; LCSC C25117
RST1: B3U-1000P; SW_B3U-1000P; LCSC C231329
SW1: B3U-1000P; SW_B3U-1000P; LCSC C231329
TP1: IO; TestPoint_Pad_D1.0mm
TP2: CLK; TestPoint_Pad_D1.0mm
TP3: GND; TestPoint_Pad_D1.0mm
TP4: RST; TestPoint_Pad_D1.0mm
TP5: CPARA; TestPoint_Pad_D1.0mm
TP6: PWM; TestPoint_Pad_D1.0mm
TP7: VCC; TestPoint_Pad_D1.0mm
TP8: 0.10; TestPoint_Pad_D1.0mm
U1: E73-2G4M08S1C
U2: SHTC3; Sensirion_DFN-4-1EP_2x2mm_P1mm_EP0.7x1.6mm; LCSC C194656
Y1: 32.768kHz; Crystal_SMD_3215-2Pin_3.2x1.5mm; LCSC C32346

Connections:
0.10: TP8.1, U1.43 (P0.10/NFC2)
+3V0: BT1.1 (+), C2.1, R7.2, R8.1, TP7.1, U1.19 (VDD), U1.23 (VDDH), U2.1 (VDD)
BTN1: SW1.1, U1.10 (P0.30/AIN6)
CPARA: D1.2 (A), Q1.2 (E), R1.2, TP5.1
GND: BT1.2 (-), C1.2, C2.2, C3.1, C4.2, D2.1 (K), Q1.3 (C), R6.2, R10.1, RST1.2, SW1.2, TP3.1, U1.5 (GND@1), U1.21 (GND@2), U2.4 (VSS)
LED: R2.2, U1.4 (P0.28/AIN4)
unnamed: D2.2 (A), R2.1
unnamed: Q1.1 (B), R4.1
unnamed: C3.2, U1.11 (P0.00/XL1), Y1.2
unnamed: C4.1, U1.13 (P0.01/XL2), Y1.1
PHOTO_OUT: Q4.2 (E), R10.2, U1.7 (P0.02/AIN0)
PHOTO_V: Q4.1 (C), U1.8 (P0.29/AIN5)
PWM: R1.1, R4.2, TP6.1, U1.15 (P0.05/AIN3)
RST: RST1.1, TP4.1, U1.26 (P0.18/RESET)
SCL: R8.2, U1.33 (P0.13), U2.2 (SCL)
SDA: R7.1, U1.35 (P0.24), U2.3 (SDA)
SENS_OUT: C1.1, D1.1 (K), R6.1, U1.3 (P0.03/AIN1)
SWDCLK: TP2.1, U1.39 (SWDCLK)
SWDIO: TP1.1, U1.37 (SWDIO)

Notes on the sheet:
Fast discharge on PWM’s low cycle
Temperature and humidity sensor
LED
nRF52 module
Parasitic capacitor sensing
Test pads
Light sensor
Reset switch
User button
Battery clip

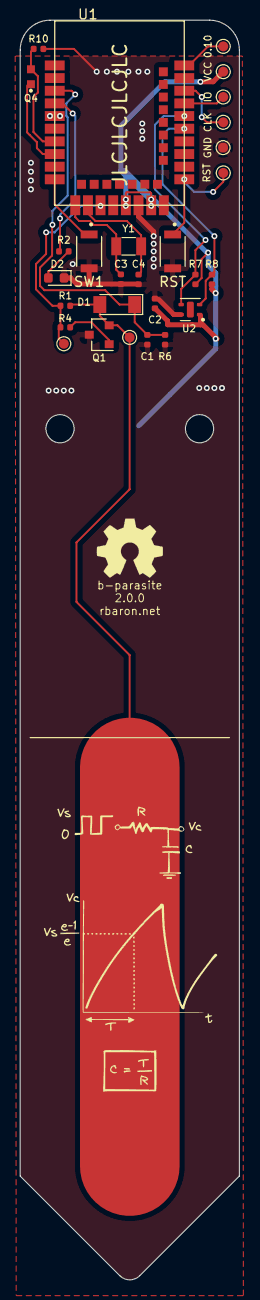
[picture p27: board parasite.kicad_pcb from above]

Board: 2 copper layers, 22.0 x 126.4 mm, 29 parts (1 on the bottom side), 19 nets.

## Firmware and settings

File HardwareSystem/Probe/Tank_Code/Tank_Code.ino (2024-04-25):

/*
  Tank code
  Handles connecting the the probe bluetooth signal and sending it to the server
*/

#include <SPI.h>
#include <ArduinoBLE.h>
#include <WiFi.h>
#include <HTTPClient.h>
#include <Arduino_JSON.h>

//----------------------------------------------------------------------------------------------------------------------
// WiFi
//----------------------------------------------------------------------------------------------------------------------

///////TODO: Put Wifi Username and Password
char ssid[32] = "SP10"; //Need to be 2 GHz
char pass[32] = "319valvano"; //INSERT WIFI PASSWORD;         //Change wifi password
char* systemID = "a2h87hd1";

//TODO: Update serverName

const char* IP = "http://192.168.137.7:5000";
char serverName[70];
char getServerName[70];


String sensorReadings;
int sensorReadingsArr[3];

//----------------------------------------------------------------------------------------------------------------------
// BLE UUIDs
//----------------------------------------------------------------------------------------------------------------------

// https://www.bluetooth.com/specifications/gatt/services/
// https://www.bluetooth.com/specifications/gatt/characteristics/

static String    serviceUUID("4fafc201-1fb5-459e-8fcc-c5c9c331914b");
static String    charUUID("beb5483e-36e1-4688-b7f5-ea07361b26a8");
static char*    charMoistUUID("fb6cf981-31cc-4f36-af06-1f2f3e919840");
static char*    charTempUUID("35b17f66-73d1-4c92-92f6-9032ef1987d3");
static char*    charLightUUID("3cab9341-e65b-46e9-83ed-c8a7f2f841c2");
static char*    charHumUUID("f3b857d0-1e8a-4dff-a941-9ea9a3594275");

//----------------------------------------------------------------------------------------------------------------------
//Plant Data
//----------------------------------------------------------------------------------------------------------------------

typedef struct __attribute__( ( packed ) )
{
  uint32_t moisture;
  float temp;
  uint32_t light;
  float humidity;
} plant_health;

plant_health ble_plant_health;

//----------------------------------------------------------------------------------------------------------------------
//Sensor Data
//----------------------------------------------------------------------------------------------------------------------

#define batteryLevelPin A6
int batteryLevel;

//For Ultrasonic
int sensorLoop = 0;
const int trigPin = 2;
const int echoPin = 3;
long duration;
int tankLevel;

int moistureCutoff = 2780;
int delayTime = 10;

//----------------------------------------------------------------------------------------------------------------------
// App
//----------------------------------------------------------------------------------------------------------------------

bool updateWeb = true;
bool updateHealth = true;
bool wifiActive = false;
bool bleActive = false;
bool updated = false;
bool WiFisetup = false;
bool delayStart = false;

int pumpPin = 8;              //TODO: Change pumpPin to what the pumpPin will be
int pumpActiveLength = 2;    //in seconds
int pumpActiveTimeRemaining = 0;    //This is our timer for our pump to always reference how much time is left to run, no multithreading no r/w problems (dub)

String httpRequestData = "";
WiFiClient client;
HTTPClient http;

//----------------------------------------------------------------------------------------------------------------------
// I/O
//----------------------------------------------------------------------------------------------------------------------

void setup()
{
  delay(2000);
  

  Serial.begin( 9600 );
  delay(2000);

  Serial.println( "Tank Code Setup" );

  strcat(serverName, IP);
  strcat(serverName, "/data");

  strcat(getServerName, IP);
  strcat(getServerName, "/GetInstructions?systemID=");
  strcat(getServerName, systemID);
  
  pinMode(pumpPin, OUTPUT);

  pinMode(trigPin, OUTPUT); // Sets the trigPin as an Output
  pinMode(echoPin, INPUT); // Sets the echoPin as an Input

  Serial.println( "Tank Code Starting" );
}

void loop()
{  
  delayStart = false;

  bleTask();

  if((ble_plant_health.moisture > moistureCutoff) && (updated == true)){
    updated = false;
    Serial.println( "Pump On" );
    pumpEnable(pumpActiveLength);
  }

  if(sensorLoop == 0){
    Serial.println( "getting PeriodicUpdate" );
    PeriodicUpdate();
  }
  sensorLoop = (sensorLoop + 1) % 10;

  wifiTask();

  delay(1000);

  if(delayStart == true){
    delay(delayTime * 60 * 1000);
  }
}


//==================================================================
//Use This one for only enabling for burst amount of seconds at a time but will be reoccuring, meaning we will constantly come back until the clock expires
#define dutyCycle 1000/2   //50% duty cycle

void pumpEnable(int seconds)
{
  pumpActiveTimeRemaining = seconds * 1000;
  while((pumpActiveTimeRemaining != 0) ){
    Serial.println( "Pump High" );
    digitalWrite(pumpPin, HIGH);
    delayMicroseconds(dutyCycle);
    pumpActiveTimeRemaining--;
  }
  digitalWrite(pumpPin, LOW);
}

void wifiTask( void )
{
  enum WIFI_STATE_TYPE { WIFI_STATE_OFF,
                         WIFI_STATE_CONNECT,
                         WIFI_STATE_SEND,
                         WIFI_STATE_RECIEVE,
                         WIFI_STATE_END,
                         WIFI_STATE_RESTART = 255
                       };

  static int state = WIFI_STATE_OFF;
  static int wifiConnectTry = 0;
  static int wifiStatus = WL_IDLE_STATUS;

  switch ( state )
  {
    case WIFI_STATE_OFF:
      if ( updateWeb && ! bleActive )
      {
        wifiActive = true;
        updateWeb = false;
        Serial.println( "WiFi active" );
        state++;
        break;
      }
      break;
    case WIFI_STATE_CONNECT:
      if ( WiFi.isConnected() )
      {
        Serial.println( "WiFi connected" );
        state++;
        break;
      }
      if ( wifiConnectTry > 10 )
      {
        // could not connect, clear everything and try again later
        state = WIFI_STATE_RESTART;
        break;
      }
      WiFi.mode(WIFI_STA);
      wifiStatus = WiFi.begin( ssid, pass );
      delay(1000);
      wifiConnectTry++;
      Serial.print( "Try: " );
      Serial.print( wifiConnectTry );
      Serial.print( " Status: " );
      Serial.println( wifiStatus );
      break;
    case WIFI_STATE_SEND:
    {
      http.begin(client, serverName);

      http.addHeader("Content-Type", "application/json");
      int httpResponseCode = http.POST("{\"systemID\":\"" + String(systemID) + "\",\"tank_level\":" + String(tankLevel) + ",\"battery_level\":" + String (batteryLevel) + ",\"probes\":[{\"moisture\":" + String(ble_plant_health.moisture) + ",\"temp\":" + String(ble_plant_health.temp) + ",\"light\":" + String(ble_plant_health.light) + ",\"humidity\":" + String(ble_plant_health.humidity) + "}]}");

      //httpResponseCode = http.POST(httpRequestData);
      Serial.println( "http posted" );
      http.end();
      Serial.print("HTTP Response code: ");
      Serial.println(httpResponseCode);
      if(httpResponseCode == 500){
        state = WIFI_STATE_SEND;
        break;
      }
      state++;
      break;
    }
    case WIFI_STATE_RECIEVE:
    {
      http.begin(client, getServerName);
      //int httpResponseCode = http.POST("{\"systemID\":\"" + String(systemID) + "\}");
      int httpResponseCode = http.GET();
      String payload = "{}"; 
      if (httpResponseCode>0) {
        Serial.print("HTTP Response code: ");
        Serial.println(httpResponseCode);
        payload = http.getString();
      }
      else {
        Serial.print("Error code: ");
        Serial.println(httpResponseCode);
        http.end();
        state++;
        break;
      }
      // Free resources
      http.end();

      Serial.println(payload);
      JSONVar myObject = JSON.parse(payload);

      if (JSON.typeof(myObject) == "undefined") {
        Serial.println("Parsing input failed!");
        state++;
        break;
      }
    
      Serial.print("JSON object = ");
      Serial.println(myObject);
    
      // myObject.keys() can be used to get an array of all the keys in the object
      JSONVar keys = myObject.keys();
    
      for (int i = 0; i < keys.length(); i++) {
        JSONVar value = myObject[keys[i]];
        Serial.print(keys[i]);
        Serial.print(" = ");
        Serial.println(value);
        sensorReadingsArr[i] = int(value);
      }
      Serial.print("1 = ");
      Serial.println(sensorReadingsArr[0]);
      if(sensorReadingsArr[0] == -1){
        Serial.println( "Device not registered by server" );
        state++;
        break;
      }
      delayTime = sensorReadingsArr[0];
      Serial.print("2 = ");
      Serial.println(sensorReadingsArr[1]);
      moistureCutoff = sensorReadingsArr[1];
      Serial.print("3 = ");
      Serial.println(sensorReadingsArr[2]);
      pumpActiveLength = sensorReadingsArr[2];
      Serial.print("4 = ");
      Serial.println(sensorReadingsArr[3]);
      pumpEnable(sensorReadingsArr[3]);
      state++;
      break;
    }
    case WIFI_STATE_END:
      state = WIFI_STATE_OFF;
      wifiConnectTry = 0;
      wifiStatus = WL_IDLE_STATUS;
      WiFi.disconnect();
      wifiActive = false;
      updateHealth = true;
      delayStart = true;
      Serial.println( "WiFi end" );
      break;
    default:
      state = WIFI_STATE_CONNECT;
      wifiConnectTry = 0;
      wifiStatus = WL_IDLE_STATUS;
      WiFi.disconnect();
      Serial.println( "WiFi restart" );
      break;
  }
}

void bleTask( void )
{
  enum BLE_STATE_TYPE { BLE_STATE_OFF,
                        BLE_STATE_BEGIN,
                        BLE_STATE_START_SCAN,
                        BLE_STATE_SCAN,
                        BLE_STATE_STOP_SCAN,
                        BLE_STATE_PERIPHERAL_CONNECT,
                        BLE_STATE_PERIPHERAL_DISCOVER,
                        BLE_STATE_PERIPHERAL_READ,
                        BLE_STATE_END,
                        BLE_STATE_RESTART = 255
                      };

#define BLE_SCAN_TIMEOUT 10000

  static int state = BLE_STATE_OFF;
  static BLEDevice peripheral;

  switch ( state )
  {
    case BLE_STATE_OFF:
      if ( updateHealth && ! wifiActive )
      {
        bleActive = true;
        updateHealth = false;
        Serial.println( "BLE active" );
        state++;
        break;
      }
      break;
    case BLE_STATE_BEGIN:
      if ( !BLE.begin() )
      {
        Serial.println( "Starting BLE failed!" );
        break;
      }
      state++;
      break;
    case BLE_STATE_START_SCAN:
      BLE.scanForUuid( serviceUUID );
      Serial.println( "BLE_STATE_START_SCAN" );
      state++;
      break;
    case BLE_STATE_SCAN:
      peripheral = BLE.available();
      if ( !peripheral )
      {
        Serial.println( "no peripheral found" );
        break;
      }
      if ( peripheral.localName() != "SP10Server" )
      {
        Serial.println( "SP10Server not found" );
        break;
      }
      state++;
      Serial.println( "SP10Server found" );
      break;
    case BLE_STATE_STOP_SCAN:
      BLE.stopScan();
      state++;
      break;
    case BLE_STATE_PERIPHERAL_CONNECT:
      if ( !peripheral.connect() )
      {
        state = BLE_STATE_START_SCAN;
      }
      state++;
      break;
    case BLE_STATE_PERIPHERAL_DISCOVER:
      if ( !peripheral.discoverAttributes() )
      {
        peripheral.disconnect();
        state = BLE_STATE_START_SCAN;
      }
      state++;
      break;
    case BLE_STATE_PERIPHERAL_READ:
      {
        BLECharacteristic CharacteristicMoist = peripheral.characteristic( charMoistUUID );
        if ( CharacteristicMoist.readValue(&ble_plant_health.moisture, 16) == 0 )             //TODO: Characteristics data is not being acurately read, but is accurate when looking at bluetooth through other devices
        {
          Serial.println("Failed to find our characteristic Moisture UUID");
          break;
        }
        Serial.println("Found our characteristic Moisture UUID");

        BLECharacteristic CharacteristicLight = peripheral.characteristic( charLightUUID );
        if ( CharacteristicLight.readValue(&ble_plant_health.light, 16) == 0 )
        {
          Serial.println("Failed to find our characteristic Light UUID");
          break;
        }
        Serial.println("Found our characteristic Ligh UUID");

        BLECharacteristic CharacteristicHum = peripheral.characteristic( charHumUUID );
        if ( CharacteristicHum.readValue(&ble_plant_health.humidity, 16) == 0 )
        {
          Serial.println("Failed to find our characteristic Humidity UUID");
          break;
        }
        Serial.println("Found our characteristic Humidity UUID");

        BLECharacteristic CharacteristicTemp = peripheral.characteristic( charTempUUID );
        if ( CharacteristicTemp.readValue(&ble_plant_health.temp, 16) == 0 )
        {
          Serial.println("Failed to find our characteristic Temperature UUID");
          break;
        }
        Serial.println("Found our characteristic Temperature UUID");

        Serial.print("Humidity:");
        Serial.println(ble_plant_health.humidity);
        Serial.print("Light:");
        Serial.println(ble_plant_health.light);
        Serial.print("Moisture:");
        Serial.println(ble_plant_health.moisture);
        Serial.print("Temperature:");
        Serial.println(ble_plant_health.temp);
        updated = true;
      }
      state++;
      break;
    case BLE_STATE_END:
      state = BLE_STATE_OFF;
      BLE.end();
      bleActive = false;
      updateWeb = true;
      Serial.println( "BLE end" );
      break;
    default:
      state = BLE_STATE_OFF;
      BLE.end();
      bleActive = false;
      Serial.println( "BLE end" );
      break;
  }
}

void PeriodicUpdate(){
  batteryLevel = analogRead(batteryLevelPin);
  Serial.print("Battery Level: ");
  Serial.println(batteryLevel);
  digitalWrite(trigPin, LOW);
  delayMicroseconds(2);
  digitalWrite(trigPin, HIGH);
  delayMicroseconds(10);
  digitalWrite(trigPin, LOW);
  duration = pulseIn(echoPin, HIGH);
  tankLevel = duration * 0.034 / 2;
  Serial.print("Tank Level: ");
  Serial.println(tankLevel);
}

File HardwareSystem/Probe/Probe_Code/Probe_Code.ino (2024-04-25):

/*
Creators: Evan LeBel, Ian Skillman, Jaime Sanchez, Rodrigo Romero
Date: 3/25/2024

FOR THIS CODE YOU NEED LIBRARY "Adafruit AHTX0"

Connectors:
Temp & Humid Sensor: Connect Vin to 3.3V, GND to GND, SCL to A5, SDA to A4
PhotoResistor: Connect A1 to voltage going from photoresistor to gnd. Circuit is from 3.3V to PhotoResistor to Resistor to GND
UltraSonic: Connect GND to GND, Echo to D10, Trig to D9, and VCC to VBUS
Soil: Connect A Pin connects to A0, + Pin connects to 3.3V, - Pin connects to GND
*/

#include <Adafruit_AHTX0.h>
#include <BLEDevice.h>
#include <BLEUtils.h>
#include <BLEServer.h>
#include <Wire.h>

#define SERVICE_UUID        "4fafc201-1fb5-459e-8fcc-c5c9c331914b"
#define CHARACTERISTIC_MOIST_UUID "fb6cf981-31cc-4f36-af06-1f2f3e919840"
#define CHARACTERISTIC_TEMP_UUID "35b17f66-73d1-4c92-92f6-9032ef1987d3"
#define CHARACTERISTIC_LIGHT_UUID "3cab9341-e65b-46e9-83ed-c8a7f2f841c2"
#define CHARACTERISTIC_HUM_UUID "f3b857d0-1e8a-4dff-a941-9ea9a3594275"

#define wetSoil 2600   // Define max value we consider soil 'wet'
#define drySoil 2900   // Define min value we consider soil 'dry'
#define bright 1500

// Define analog input
#define MoisturePin A0
#define LightPin A1

// makes the chracteristic globlal
static BLECharacteristic *pCharacteristicMoist;
static BLECharacteristic *pCharacteristicTemp;
static BLECharacteristic *pCharacteristicHum;
static BLECharacteristic *pCharacteristicLight;
BLEServer* pServer = NULL;
bool deviceConnected = false;
bool oldDeviceConnected = false;
sensors_event_t humidity, temp;  
uint32_t moisture, light;

Adafruit_AHTX0 aht;

class MyServerCallbacks: public BLEServerCallbacks {
    void onConnect(BLEServer* pServer) {
      deviceConnected = true;
      BLEDevice::startAdvertising();
    };

    void onDisconnect(BLEServer* pServer) {
      deviceConnected = false;
    }
};

void setup() {
  delay(2000);

  Serial.begin(115200);

  delay(2000);

  //Temp & Humidity Sensor setup:
  
  Serial.println("Adafruit AHT10/AHT20 demo!");
  if (! aht.begin()) {
    Serial.println("Could not find AHT? Check wiring");
    while (1) delay(10);  
  }
  Serial.println("AHT10 or AHT20 found");
  

  Serial.println("Starting BLE work!");

  BLEDevice::init("SP10Server");
  pServer = BLEDevice::createServer();
  pServer->setCallbacks(new MyServerCallbacks());
  BLEService *pService = pServer->createService(SERVICE_UUID);
  pCharacteristicMoist = pService->createCharacteristic(
                                         CHARACTERISTIC_MOIST_UUID,
                                         BLECharacteristic::PROPERTY_READ |
                                         BLECharacteristic::PROPERTY_WRITE
                                       );
  pCharacteristicTemp = pService->createCharacteristic(
                                         CHARACTERISTIC_TEMP_UUID,
                                         BLECharacteristic::PROPERTY_READ |
                                         BLECharacteristic::PROPERTY_WRITE
                                       );
  pCharacteristicLight = pService->createCharacteristic(
                                         CHARACTERISTIC_LIGHT_UUID,
                                         BLECharacteristic::PROPERTY_READ |
                                         BLECharacteristic::PROPERTY_WRITE
                                       );
  pCharacteristicHum = pService->createCharacteristic(
                                         CHARACTERISTIC_HUM_UUID,
                                         BLECharacteristic::PROPERTY_READ |
                                         BLECharacteristic::PROPERTY_WRITE
                                       );
  pService->start();
  // BLEAdvertising *pAdvertising = pServer->getAdvertising();  // this still is working for backward compatibility
  BLEAdvertising *pAdvertising = BLEDevice::getAdvertising();
  pAdvertising->addServiceUUID(SERVICE_UUID);
  pAdvertising->setScanResponse(true);
  pAdvertising->setMinPreferred(0x06);  
  pAdvertising->setMinPreferred(0x12);
  BLEDevice::startAdvertising();
  Serial.println("Characteristic defined!");
}

void ReadLight(){
  light = analogRead(LightPin);
  //light = 0;

  Serial.println("Light Value: ");
  Serial.println(light);

  if (light > bright) {
    Serial.println("Light Level High");
  } else {
    Serial.println("Light Level Low");
  }
}

void ReadMoisture(){
  moisture = analogRead(MoisturePin);

  Serial.print("Moisture Value: ");
  Serial.println(moisture);

  if (moisture < wetSoil) {
    Serial.println("Status: Soil is too wet");
  } else if (moisture >= wetSoil && moisture < drySoil) {
    Serial.println("Status: Soil moisture is perfect");
  } else {
    Serial.println("Status: Soil is too dry - time to water!");
  }
}

void ReadTemp(){

  aht.getEvent(&humidity, &temp);// populate temp and humidity objects with fresh data

  Serial.print("Temperature: "); 
  Serial.print(((temp.temperature * 9) + 3) / 5 + 32); //farenheight 
  Serial.println(" degrees F");  
  Serial.print(temp.temperature); //celcius
  Serial.println(" degrees C");
  Serial.print("Humidity: ");
  Serial.print(humidity.relative_humidity); 
  Serial.println("% rH");
}

void loop() {
  Serial.print("================================="); 
  ReadMoisture();
  ReadLight();
  ReadTemp();

  if (deviceConnected) {
    pCharacteristicMoist->setValue(moisture);//setValue takes uint8_t, uint16_t, uint32_t, int, float, double and string
    pCharacteristicTemp->setValue(temp.temperature);
    pCharacteristicLight->setValue(light);
    pCharacteristicHum->setValue(humidity.relative_humidity);
  }
  // disconnecting
  if (!deviceConnected && oldDeviceConnected) {
    delay(500); // give the bluetooth stack the chance to get things ready
    pServer->startAdvertising(); // restart advertising
    Serial.println("start advertising");
    oldDeviceConnected = deviceConnected;
  }
  // connecting
  if (deviceConnected && !oldDeviceConnected) {
    oldDeviceConnected = deviceConnected;
  }

  delay(1 * 1000 * 60);     //delay 1 minutes
}

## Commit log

2024-02-19 Create Probe
    Creating files
2024-02-24 Added testing sensor testing files and probe kicad proj
    Files added:
    ATH20 Sessor code,
    Capacitive moisture sensor,
    Initial Kicad PCB project for probe
    [parasite-B_Cu.gbr, parasite-B_Mask.gbr, parasite-B_Paste.gbr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]
2024-02-26 All Sensors in one Arduino File
2024-02-28 file repath
    [COM-16473.stp, PCB_Probe.kicad_pcb, PCB_Probe.kicad_sch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]
2024-02-28 PCB probe WIP
    [BH9VPC.step, PCB_Probe.kicad_sch]
2024-02-28 pump pcb
    [PCB_Pump.kicad_pcb, PCB_Pump.kicad_sch]
2024-02-28 Login Progress (Syncing/Login Button/User Type)
2024-02-29 Added more circuits to PCB probe
    Added more circuits to PCB probe
    [161.step, LP0003A.stp, PCB_Probe.kicad_pcb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]
2024-03-01 more layout design
    Added:
    header footprint
    pcb margins for probe
    [PCB_Probe.kicad_pcb, PRT-16279.stp]
2024-03-02 PCB Probe layout
    working on pcb probe layout
    [PCB_Probe.kicad_pcb, PCB_Probe.kicad_sch]
2024-03-02 pump pcb work
    [PCB_Pump.kicad_pcb, PCB_Pump.kicad_sch]
2024-03-02 esp32 model
2024-03-02 Routing and Placement for Probe PCB
    [PCB_Probe.kicad_pcb, PCB_Probe.kicad_sch]
2024-03-03 finished PCB pump
    [PCB_Pump.kicad_pcb, PCB_Pump.kicad_sch]
2024-03-04 pcb pump revision
    [PCB_Pump.kicad_pcb, PCB_Pump.kicad_sch]
2024-03-04 updated Probe schematic look
    [PCB_Probe.kicad_pcb, PCB_Probe.kicad_sch]
2024-03-06 added functionality to join button for demo purposes
2024-03-06 updated ground plane footprint
    [PCB_Probe.kicad_pcb, PCB_Probe.kicad_sch]
2024-03-07 removed redundant 3V LDO
    [PCB_Probe.kicad_pcb, PCB_Probe.kicad_sch]
2024-03-08 pumpv3-added some symbols
    [PCB_Pump.kicad_pcb]
2024-03-08 updates on both boards
    [PCB_Probe.kicad_pcb, PCB_Pump.kicad_pcb, PCB_Pump.kicad_sch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]
2024-04-05 battery level example code
2024-04-05 Battery Level sensor and testing bluetooth stuff
2024-04-10 changed buck wiring
    [PCB_Pump.kicad_sch]
2024-04-10 added landing page, but still incomplete
2024-04-11 added landing page to routes
2024-04-11 fixed some comments i screwed up
    [Tank_Code.ino]
2024-04-11 3d models
    [15-Pin Header - Female - 2.54mm.step, Hub_Bottom.3mf, Hub_Bottom.stl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]
2024-04-11 Exapansion of HW interaction, sys_user_invite bug fix, ground work for noti and sys_users func, file reformatting
2024-04-11 route for a watering button is been set up
2024-04-11 Accounting for unregistered device and advancing states
2024-04-11 added Login button to home page
2024-04-12 made some changes to homescreen landing page
2024-04-12 new bottom hub 3d model
    [Hub_Bottom_Walls.3mf]
2024-04-12 modified team section on landing page
2024-04-14 updated 3d model
    [New_bottom_half.3mf]
2024-04-25 New setting parameter pumpActiveLength is available
2024-04-25 Developed Plant Settings (Button On Dashboard Doesn't Work Yet)
2024-04-25 battery_level data point, new settings param,
2024-04-28 Landing Page Changes
2024-04-28 Battery Measurmenet Update
2024-04-29 Battery Life Reading On Dashboard
2024-04-29 Added Water Button
